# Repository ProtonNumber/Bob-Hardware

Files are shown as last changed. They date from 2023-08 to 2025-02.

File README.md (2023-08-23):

# Bob!

This is the Kicad Repo for Bob, an open-source flight computer and data logger
for model rocketry.

## Specification
- MCU: Raspberry Pi [RP2040](https://datasheets.raspberrypi.com/rp2040/rp2040-datasheet.pdf) Dual Core Cortex M0+.
- Flash: 2 x Wimbond [W25Q128](https://www.winbond.com/resource-files/W25Q128JV%20RevI%2008232021%20Plus.pdf) 16 MiB Flash chips.
- IMU: QST [QMI8658C](https://www.qstcorp.com/upload/pdf/202301/13-52-25%20QMI8658A%20Datasheet%20Rev%20A.pdf) 16 G / 2048 DPS IMU
- Compass: QST [QMC5883L](https://datasheet.lcsc.com/szlcsc/QST-QMC5883L-TR_C192585.pdf)
- Barometer: HopeRF [HP203B](https://hoperf.com/data/upload/portal/20190307/HP203B_DataSheet_EN_V2.0.pdf)
- GPIO: 16 GPIO pins broken out, plus access to internal I2C bus.
- Pyro: 2 x Pyro channels with continuity detection and separate arming switch.

## Pin Assignments
| GPIO Pin | Usage | Broken Out? | Notes |
|---|---|---|---|
| GPIO 00  | - | Y | |
| GPIO 01  | - | Y | |
| GPIO 02  | - | Y | |
| GPIO 03  | - | Y | |
| GPIO 04  | - | Y | |
| GPIO 05  | - | Y | |
| GPIO 06  | - | Y | |
| GPIO 07  | Fire Main | N | |
| GPIO 08  | Fire Drogue | N | |
| GPIO 09  | Compass Interrupt | N | |
| GPIO 10  | IMU Interrupt 1 | N | |
| GPIO 11  | IMU Interrupt 2 | N | |
| GPIO 12  | I2C SDA | Y | |
| GPIO 13  | I2C SCL | Y | |
| GPIO 14  | Drogue Continuity | N | |
| GPIO 15  | Main Continuity | N | |
| GPIO 16  | Flash SPI RX | N | |
| GPIO 17  | Flash SPI CS | N | |
| GPIO 18  | Flash SPI SCLK | N | |
| GPIO 19  | Flash SPI TX | N | |
| GPIO 20  | Buzzer | N | Buzzer is only powered when battery is connected. |
| GPIO 21  | Arming Signal | Y | Reads status of the ARM switch |
| GPIO 22  | - | Y | |
| GPIO 23  | - | Y | |
| GPIO 24  | - | Y | |
| GPIO 25  | Status LED | N | |
| GPIO 26  | - | Y | May be used as analogue input |
| GPIO 27  | - | Y | May be used as analogue input |
| GPIO 28  | - | Y | May be used as analogue input |
| GPIO 29  | - | Y | May be used as analogue input |

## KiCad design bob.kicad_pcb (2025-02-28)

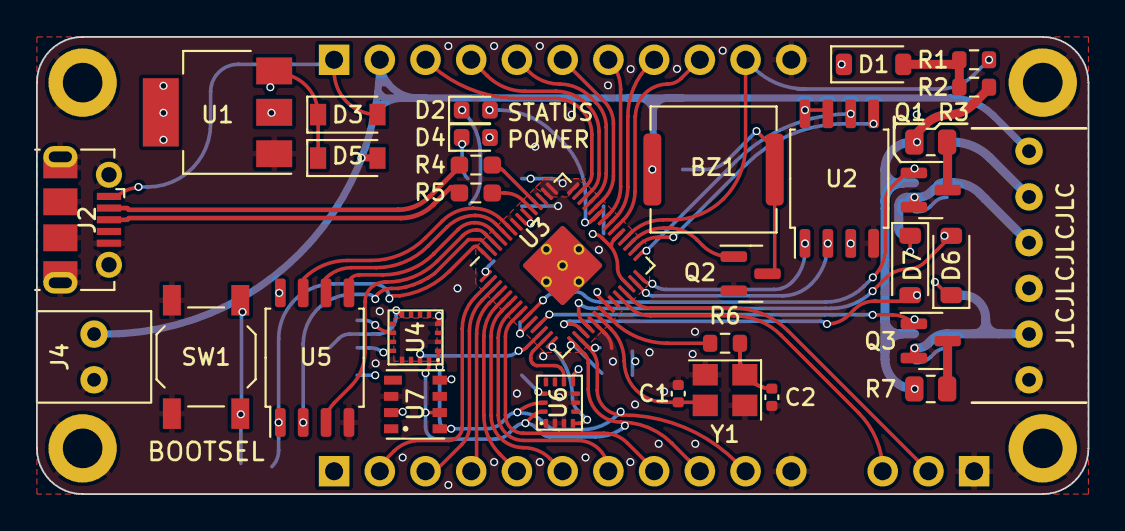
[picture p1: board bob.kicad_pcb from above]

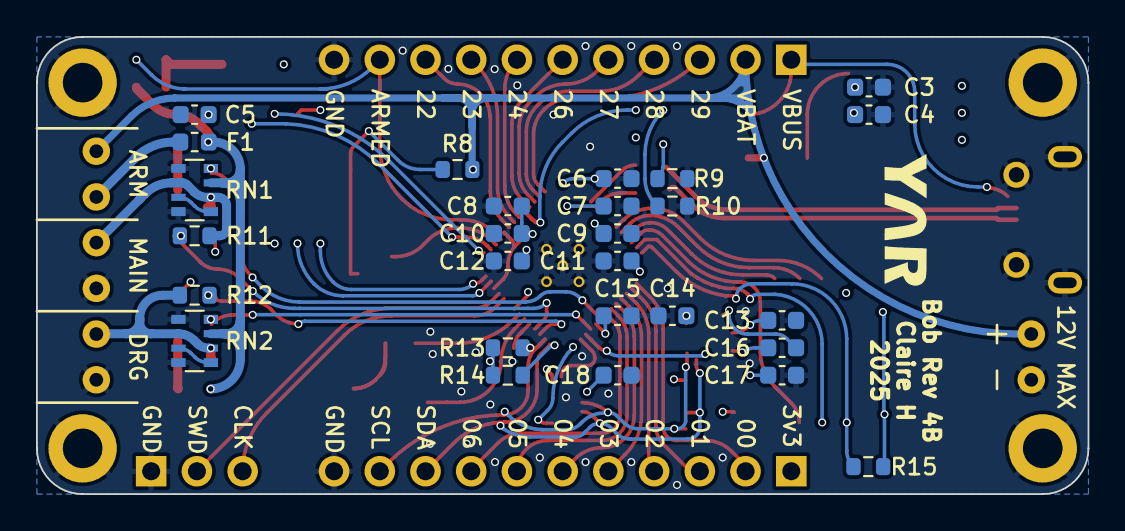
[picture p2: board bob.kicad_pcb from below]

Board: 4 copper layers, 58.4 x 25.4 mm, 67 parts (28 on the bottom side), 67 nets.

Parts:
BZ1: Buzzer; CPT-7502-65-SMT-TR
C1, C2: 7p; C_0402_1005Metric
C3, C4: 10u; C_0603_1608Metric
C5, C8, C9, C10, C11, C12, C14, C15, C17, C18: 100n; C_0603_1608Metric
C6, C7: 1u; C_0603_1608Metric
C13: 4.7u; C_0603_1608Metric
C16: 220n; C_0603_1608Metric
D1, D3, D5, D6, D7: B5819W SL; D_SOD-123
D2: GREEN; LED_0603_1608Metric
D4: RED; LED_0603_1608Metric
F1: Polyfuse; Fuse_0603_1608Metric
H1, H2, H3, H4: MountingHole_Pad; MountingHole_2.2mm_M2_DIN965_Pad
J1, J6: GPIO (Optional); PinHeader_1x11_P2.54mm_Vertical
J2: Micro USB Female; USB_Micro-B_Molex-105017-0001
J3: Conn_01x06_Pin; ScrewTerm_2.54x06
J4: Screw Terminal, 2.54mm; ScrewTerm_2.54x02
J5: Conn_01x03_Male; PinHeader_1x03_P2.54mm_Vertical
Q1, Q2, Q3: AO3400A; SOT-23
R1, R2, R13, R14: 3k6; R_0603_1608Metric
R3, R7: 5; R_0805_2012Metric
R4, R5: 27; R_0603_1608Metric_Pad0.98x0.95mm_HandSolder
R6, R8, R15: 1k; R_0603_1608Metric
R9: 470; R_0603_1608Metric
R10: 220; R_0603_1608Metric
R11, R12: 10k; R_0603_1608Metric
RN1, RN2: 10k; R_Array_Convex_4x0603
SW1: Bootsel; SW_SPST_TL3342
U1: AMS1117-3.3; SOT-223-3_TabPin2
U2, U5: W25Q128JVSS; SOIC-8_5.23x5.23mm_P1.27mm
U3: RP2040; RP2040-QFN-56
U4: QMC5883L; QMC5883L-LGA16
U6: QMI8658C; QMI8658C-LGA14
U7: HP203B; HP203B-LGA8
Y1: 12MHz; Crystal_SMD_3225-4Pin_3.2x2.5mm
YAR: LOGO; yar_new

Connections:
+1V1: C7.1, C12.1, U3.23 (DVDD), U3.45 (VREG_VOUT), U3.50 (DVDD)
+3V3: C4.1, C5.1, C6.1, C8.1, C9.1, C10.1, C11.1, C14.1, C15.1, C17.1, C18.1, D1.1 (K), D4.2 (A), D6.1 (K), D7.1 (K), J6.1, R13.2, R14.2, U1.2 (VO), U2.3 (IO2), U2.7 (IO3), U2.8 (VCC), U3.1 (IOVDD), U3.10 (IOVDD), U3.22 (IOVDD), U3.26 (RUN), U3.33 (IOVDD), U3.42 (IOVDD), U3.43 (ADC_AVDD), U3.44 (VREG_IN), U3.48 (USB_VDD), U3.49 (IOVDD), U4.2 (VDD), U4.4 (S1), U4.13 (VIO), U5.8 (VCC), U6.8 (VDD), U6.12 (CS), U7.3 (VDD), U7.8 (CSB)
+BATT: BZ1.1 (-), D5.2 (A), J1.2, J3.6, J4.2, R8.2
/Pyro 1/Fire +: J3.4, Q1.2 (S), R11.1, RN1.2 (R2.1), RN1.6 (R3.2)
/Pyro 2/Fire +: J3.2, Q3.2 (S), R12.1, RN2.2 (R2.1), RN2.6 (R3.2)
ARM: F1.2, R2.2, R3.1, R7.1, RN1.7 (R2.2), RN2.7 (R2.2)
ARMED: J1.10, R1.1, U3.32 (GPIO21)
BUZZER: Q2.1 (G), U3.31 (GPIO20)
Cont 1: D6.2 (A), R11.2, U3.18 (GPIO15)
Cont 2: D7.2 (A), R12.2, U3.17 (GPIO14)
GND: C1.1, C2.1, C3.2, C4.2, C5.2, C6.2, C7.2, C8.2, C9.2, C10.2, C11.2, C12.2, C13.1, C14.2, C15.2, C17.2, C18.2, H1.1, H2.1, H3.1, H4.1, J1.11, J2.5 (GND), J2.6 (Shield), J3.1, J3.3, J4.1, J5.1, J6.11, Q2.2 (S), R9.1, R10.2, RN1.1 (R1.1), RN1.4 (R4.1), RN2.1 (R1.1), RN2.4 (R4.1), SW1.1, U1.1 (GND), U2.4 (GND), U3.19 (TESTEN), U3.57 (GND), U4.9 (GND), U4.11 (GND), U5.4 (GND), U6.1 (SDO/SA0), U6.2 (SDX), U6.3 (SCX), U6.6 (GND), U6.7 (GND), U7.2 (GND), Y1.2, Y1.4
GPIO0: J6.2, U3.2 (GPIO0)
GPIO1: J6.3, U3.3 (GPIO1)
GPIO2: J6.4, U3.4 (GPIO2)
GPIO3: J6.5, U3.5 (GPIO3)
GPIO4: J6.6, U3.6 (GPIO4)
GPIO5: J6.7, U3.7 (GPIO5)
GPIO6: J6.8, U3.8 (GPIO6)
GPIO22: J1.9, U3.34 (GPIO22)
GPIO23: J1.8, U3.35 (GPIO23)
GPIO24: J1.7, U3.36 (GPIO24)
GPIO26: J1.6, U3.38 (GPIO26_ADC0)
GPIO27: J1.5, U3.39 (GPIO27_ADC1)
GPIO28: J1.4, U3.40 (GPIO28_ADC2)
GPIO29: J1.3, U3.41 (GPIO29_ADC3)
I2C_SCL: J6.10, R13.1, U3.16 (GPIO13), U4.1 (SCL), U6.13 (SCL), U7.5 (SCL)
I2C_SDA: J6.9, R14.1, U3.15 (GPIO12), U4.16 (SDA), U6.14 (SDA), U7.6 (SDA)
unnamed: BZ1.2 (+), Q2.3 (D), R8.1
unnamed: C2.2, R6.1, Y1.1
unnamed: C3.1, D3.1 (K), D5.1 (K), U1.3 (VI)
unnamed: D2.2 (A), U3.37 (GPIO25)
unnamed: D2.1 (K), R10.1
unnamed: D4.1 (K), R9.2
unnamed: D1.2 (A), R1.2, R2.1
unnamed: F1.1, J3.5
unnamed: Q1.3 (D), R3.2
unnamed: Q3.3 (D), R7.2
unnamed: R15.1, SW1.2
unnamed: RN1.3 (R3.1), RN1.5 (R4.2)
unnamed: RN2.3 (R3.1), RN2.5 (R4.2)
unnamed: C13.2, U4.10 (C1)
unnamed: C16.2, U4.12 (SETC)
unnamed: C16.1, U4.8 (SETP)
unnamed: R4.1, U3.46 (USB_DM)
unnamed: R5.1, U3.47 (USB_DP)
unnamed: C1.2, U3.20 (XIN), Y1.3
unnamed: R6.2, U3.21 (XOUT)
Pyro 1: Q1.1 (G), RN1.8 (R1.2), U3.9 (GPIO7)
Pyro 2: Q3.1 (G), RN2.8 (R1.2), U3.11 (GPIO8)
QMC_DRDY: U3.12 (GPIO9), U4.15 (DRDY)
QMI_INT1: U3.14 (GPIO11), U6.4 (INT1)
QMI_INT2: U3.13 (GPIO10), U6.9 (INT2)
QSPI_SCLK: U3.52 (QSPI_SCLK), U5.6 (CLK)
QSPI_SD0: U3.53 (QSPI_SD0), U5.5 (DI(IO0))
QSPI_SD1: U3.55 (QSPI_SD1), U5.2 (DO(IO1))
QSPI_SD2: U3.54 (QSPI_SD2), U5.3 (IO2)
QSPI_SD3: U3.51 (QSPI_SD3), U5.7 (IO3)
QSPI_SS: R15.2, U3.56 (QSPI_SS), U5.1 (~CS)
SPI_CS: U2.1 (~CS), U3.28 (GPIO17)
SPI_RX: U2.2 (DO(IO1)), U3.27 (GPIO16)
SPI_SCLK: U2.6 (CLK), U3.29 (GPIO18)
SPI_TX: U2.5 (DI(IO0)), U3.30 (GPIO19)
SWCLK: J5.3, U3.24 (SWCLK)
SWD: J5.2, U3.25 (SWD)
USB_D+: J2.3 (D+), R5.2
USB_D-: J2.2 (D-), R4.2
VBUS: D3.2 (A), J1.1, J2.1 (VBUS)

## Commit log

2022-07-04 Add kicad files
    [bob-B_Cu.gbr, bob-B_Mask.gbr, bob-B_Paste.gbr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]
2022-07-04 Removed gbr files, fixed gitignore
    [bob-B_Cu.gbr, bob-B_Mask.gbr, bob-B_Paste.gbr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]
2022-07-04 Rearranged directories
    [bob.kicad_pcb, bob.kicad_sch]
2022-07-04 Fixed issues with USB impedance
    [bob.kicad_pcb]
2022-07-24 Fixed MPU6050 charge pump cap
    [bob.kicad_sch]
2022-07-24 Replaced BMP180 with HP203B
    [bob.kicad_sch]
2022-07-24 Added piezo buzzer
    [bob.kicad_sch]
2022-07-24 Moved I2C to bottom of RP2040
    [bob.kicad_sch]
2022-07-24 Changed 0402s to 0603s
    [bob.kicad_sch]
2022-07-24 Added SWD connector and test points
    [bob.kicad_sch]
2022-07-24 Broke out VBAT
    [bob.kicad_sch]
2022-07-25 Added a magnetometer
    [bob.kicad_sch]
2022-07-28 Rev 3, issued for production
    [bob.kicad_pcb, bob.kicad_sch]
2022-07-28 Added addresses to I2C bus
    [bob.kicad_sch]
2022-07-28 Fixed issues and reissued for production
    [bob.kicad_pcb]
2022-08-22 Added address for QMC5883L
    [bob.kicad_sch]
2022-08-22 Added Kicad Libs. Added thermal relief.
    [bob.kicad_pcb]
2022-08-22 Added nice symbols to schematic
    [bob.kicad_sch]
2022-08-22 Changed LED current limiter so it wont be so bright
    [bob.kicad_sch]
2022-08-22 Changed SW1 to a button
    [bob.kicad_sch]
2022-08-22 Nope, switch wont fit :(
    [bob.kicad_sch]
2022-08-22 Updated footprints to be much saner
    [bob.kicad_sch]
2022-08-22 Changed U3 to the new symbol libs
    [bob.kicad_sch]
2022-09-07 Fixed very minor alignment issue that was annoying me.
    [bob.kicad_sch]
2022-11-08 Added pyro channels Added bendy traces Added status LED Removed buzzer
    [Pyro.kicad_sch, bob.kicad_pcb, bob.kicad_sch]
2022-11-11 Started work on bob R4
    [bob.kicad_pcb]
2023-07-08 Restructure repo
    [Pyro.kicad_sch, bob.kicad_pcb, bob.kicad_sch]
2023-08-12 Swap out components to match LCSC stock
    [bob.kicad_sch]
2023-08-12 Add dedicated flash for data
    [bob.kicad_sch]
2023-08-12 Return of the buzzer
    [bob.kicad_sch]
2023-08-23 Rev 4 issued for production
    [Pyro.kicad_sch, bob.kicad_pcb, bob.kicad_sch]
2023-08-24 Moved via from HP203 SCK pad
    [bob.kicad_pcb]
2025-02-28 Add current limit resistor between pyro channel and pin.
    [Pyro.kicad_sch]
2025-02-28 Change to piezo buzzer in stock, add parallel resistor per manufacturer's guidance
    [bob.kicad_sch]
2025-02-28 Reroute PCB to match changes in schematic
    [bob.kicad_pcb]
